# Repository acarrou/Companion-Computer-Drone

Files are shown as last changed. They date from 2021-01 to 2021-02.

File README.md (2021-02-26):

# PX4 Companion-Computer-Drone
## Introduction
This guide is meant to help people interested in making a drone using a Pixhawk as the flight controller with an onboard computer of your choice using Dronekit or ROS. This guide shows you how to use Dronekit using a Raspberry Pi and ROS with a Jetson Nano. However, they can both be done the same way with some changes. There are specific components that are needed to complete this project.

# Table of Contents
- [:one: Getting Started](#one-getting-started)
    - [Parts Required](#parts-required)
    - [Drone Assembly](#drone-assembly)
    - [Firmware](#firmware)
- [:two: The Onboard Computer](#two-the-onboard-computer)
    - [Jetson Nano (***THIS SECTION IS STILL UNDER CONSTRUCTION USE THE RASPBERRY PI FOR NOW***)](#jetson-nano)
        - [ROS Melodic Installation](#ros-melodic-installation)
        - [MAVROS Installation](#mavros-installation)
        - [Pixhawk and Jetson Nano Configuration](#pixhawk-and-jetson-nano-configuration)
        - [Jetson Nano and Pixhawk Communication](#jetson-nano-and-pixhawk-communication)
    - [Raspberry Pi](#raspberry-pi)
        - [GPIO Pin Configuration](#gpio-pin-configuration)
        - [Raspberry Pi Serial Configuration](#raspberry-pi-serial-configuration)
        - [Raspberry Pi and Pixhawk Communication](#raspberry-pi-and-pixhawk-communication)
        - [Dronekit](#dronekit)
            - [Simulation](#simulation)
            - [Running Dronekit on the Pi](#running-dronekit-on-the-pi)
            
<br><br/>

# :one: Getting Started
## Parts Required
Everything on the ***[Parts List](https://docs.google.com/document/d/1yg1S2lEn6Pxzbmr_OziczwqIsVRe4be1YQAyOio6FKI/edit?usp=sharing)*** is required for this project. Please read carefully what is needed. This is also assuming you have the necessary tools of a soldering iron, snips, and other essential tools needed for electronics.

## Drone Assembly
***[Here](https://youtube.com/playlist?list=PLm_39In9-wKMa8U90cwcDMecCGuM5Sja1)*** is a playlist of videos showing you how to build your drone. This will also go over how to flash the Firmware to the pixhawk. I will go more in-depth regarding the Firmware in the next area. You can choose either Ardupilot or PX4. However, I recommend PX4 Firmware.

Make sure your motors are in the correct configuration. You do this by making sure the motor wires are connected to the correct wires of the ESC. Below is a diagram of the direction of the motors and ESC configuration.
***I recommend you put on the propellers at the end. Not until you are ready to fly.***
<br><br/>

<br><br/>

<br><br/>


<br><br/>
Plug the ESC pins into back of the Pixhawk. (order should be from top-> -, s, +) ***Make sure they are in the correct order or your drone will fly incorrectly.***
<br><br/>

<br><br/>
Plug in the rest of  the modules you've puchased into their respected slots as showed in this image:
<br><br/>


<br><br/>

## Firmware
We are using [QGroundControl](https://docs.qgroundcontrol.com/master/en/getting_started/download_and_install.html), it works great and makes it easy to set parameters. Follow this [video](https://www.youtube.com/watch?v=BNzeVGD8IZI&t=677s) on how to install the PX4 Firmware. If you would like to use the Ardupilot firmware, click on Ardupilot in the QGroundControl options. If you have issues with the latest px4 Firmware, you can look at earlier versions [here](https://github.com/PX4/PX4-Autopilot/releases), we are currently using ***v1.10.1***.


<br><br/>

# :two: The Onboard Computer
There are two companion computers we recommend using the Jetson Nano or the Raspberry Pi. The Jetson Nano is a pricier embedded system compared to the Raspberry Pi. However, it makes an excellent system for object detection/avoidance. Make sure you have all the necessary parts to power and put an OS on these computers. You will need a device to put the OS on the micro sd card. Something like this -> ***[Micro SD Card USB Reader.](https://www.amazon.com/UGREEN-Reader-Portable-Adapter-Windows/dp/B0779V61XB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)*** This makes it easy to image.
<br/>
[nKuylen](https://github.com/nKuylen) has made a platform in the back of the drone for the Raspberry pi or Jetson Nano. We recommend printing this or developing your own.

## Jetson Nano (***THIS SECTION IS STILL UNDER CONSTRUCTION USE THE RASPBERRY PI FOR NOW***)

We will be using ROS with the Jetson Nano. If you are unfamiliar with ROS, I recommend you learn it first through the [documentation](http://wiki.ros.org/Documentation) as this part will assume you know how to operate the catkin workspace. For more information on the Jetson nano, please follow this ***[site](https://developer.nvidia.com/embedded/learn/get-started-jetson-nano-devkit)***. It would be best to use ***[Balena Etcher](https://www.balena.io/etcher/)*** for an easy imaging process. A helpful video I found is ***[here](https://www.youtube.com/watch?v=fepv1uDyiXk)***. Use the image given for the Jetson Nano ***[here](https://developer.nvidia.com/embedded/learn/get-started-jetson-nano-devkit#write)***. Once you have successfully imaged your Jetson Nano put the sd card into the Nano.
### ROS Melodic Installation
We are using ROS Melodic as the Jetson Nano is using their NVIDIA® Jetson Nano™ Developer Kit deriving from Ubuntu 18.04. This ROS install is taken from [here](http://wiki.ros.org/melodic/Installation/Ubuntu)
<br/>

Setting your sources.list
<br/>
```bash
sudo sh -c 'echo "deb http://packages.ros.org/ros/ubuntu $(lsb_release -sc) main" > /etc/apt/sources.list.d/ros-latest.list'
```
<br/>

Keys Setup:
<br/>
```bash
sudo apt-key adv --keyserver 'hkp://keyserver.ubuntu.com:80' --recv-key C1CF6E31E6BADE8868B172B4F42ED6FBAB17C654
```
<br/>

Install:
<br/>
```bash
sudo apt update
sudo apt install ros-melodic-desktop-full
```
<br/>

Environment Setup:
<br/>
```bash
echo "source /opt/ros/melodic/setup.bash" >> ~/.bashrc
source ~/.bashrc
```
<br/>

(Optional) Dependencies for Building Packages:
<br/>
```bash
sudo apt install python-rosdep python-rosinstall python-rosinstall-generator python-wstool build-essential
```
<br/>

Install rosdep:
<br/>
```bash
sudo apt install python-rosdep
```

<br/>
Initialize rosdep:
<br/>

```bash
sudo rosdep init
rosdep update
```
<br><br/>

### MAVROS Installation
***--NEED TO WORK ON THIS--*** <br/>
MAVROS is the MAVLink extendable communication node for ROS with proxy for Ground Control Station.
<br><br/>
Install MAVROS:
<br/>
```bash
sudo apt-get install ros-melodic-mavros ros-melodic-mavros-extras
```
<br><br/>
Install Geographic datasets:
<br/>
```bash
wget https://raw.githubusercontent.com/mavlink/mavros/master/mavros/scripts/install_geographiclib_datasets.sh
chmod a+x install_geographiclib_datasets.sh
sudo ./install_geographiclib_datasets.sh
```
<br><br/>

### Pixhawk and Jetson Nano Configuration
The configuration for the Pixhawk and Jetson Nano is straightforward. Use a micro USB to USB cable. Connect the micro USB side into the Pixhawk's serial port and the USB into the Jetson nano.
<br/>

<br><br/>

### Jetson Nano and Pixhawk Communication
After plugging the cord into the Pixhawk and Nano, you can run this command to see if everything is correct:
<br/>
```bash
roslaunch mavros px4.launch
```
<br/>

If there is a permissions issue with the serial port, make sure your user is in the 'dialout' group. You can do this by using this command (replace the 'enter username' with your username):
<br/>
```bash
sudo usermod -a -G dialout enter username
```
Congrats! You have successfully connected your Nano to your Pixhawk. If you are having trouble, this [video](https://www.youtube.com/watch?v=Irko6xb2qjs) may help you.
<br><br/>

## Raspberry Pi
Start by Installing the Raspberry Pi OS using Raspberry Pi Imager ***[here](https://www.raspberrypi.org/software/)***. Image the Pi with the recommended OS. You can use this ***[video](https://www.youtube.com/watch?v=y45hsd2AOpw)*** to help you image the Pi.

### GPIO Pin Configuration
In order for the Pi to communicate with the Pixhawk, we need to connect four cables. They are 5V, GND, TX, and RX. You will need to create the connector yourself. I purchased this ***[kit](https://www.amazon.com/1-25mm-Connectors-Pre-Crimped-Pixhawk-Silicone/dp/B07S18D3RN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)*** to make my own. I then soldered the connectors from the pixhawk to 4 female jumper wires.

***Here is the configuration of the pins***

<br><br/>

### Raspberry Pi Serial Configuration

On your Raspberry Pi, enter:
```bash
sudo raspi-config
```
And in the utility, select “Interfacing Options”:
<br/>

<br><br/>
RasPiConfiguration Utility
And then “Serial”:
<br/>

<br><br/>
When prompted, select ```no``` to “Would you like a login shell to be accessible over serial?”.

When prompted, select ```yes``` to “Would you like the serial port hardware to be enabled?”.

Reboot the Raspberry Pi when you are done.

The Raspberry Pi’s serial port will now be usable on ```/dev/serial0```.

<br><br/>

### Raspberry Pi and Pixhawk Communication

Once you have configured your Pi, you now have to change a few parameters on your pixhawk in QGroundControl or another ground control software. To set up the default companion computer message stream on TELEM 2, set the following parameters:
```bash
MAV_1_CONFIG = TELEM 2 (MAV_1_CONFIG is often used to map the TELEM 2 port)
MAV_1_MODE = Onboard
SER_TEL2_BAUD = 921600 (921600 or higher recommended for applications like log streaming or FastRTPS)
```

After you have changed those parameters, restart the Pixhawk. If not done already, connect the Raspberry Pi to the Pixhawk. You will need to install MAVProxy dependencies. You can find the MAVProxy install here -> [MAVProxy INSTALL GUIDE](https://ardupilot.org/mavproxy/docs/getting_started/download_and_installation.html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). I will show below how to install these dependencies for Python 2 since that is what the Pi has on default.

For Python 2 on Debian based systems (including Ubuntu, WSL, Raspian):
<br/>
```bash 
sudo apt-get install python-dev python-opencv python-wxgtk4.0 python-pip python-matplotlib python-lxml python-pygame
pip install PyYAML mavproxy --user
echo "export PATH=$PATH:$HOME/.local/bin" >> ~/.bashrc
```

If you get a “permission denied” error message when connecting to serial devices, the user permissions may need to be changed:
<br/>
```bash 
sudo usermod -a -G dialout <username>
```

Make sure you update:
<br/>
```bash
pip install mavproxy --user --upgrade
```
Once finished installing everything, make sure to reboot the Pi.
<br><br/>

Next, run this command in the terminal to test the serial connection between the Pi and Pixhawk. If you are only getting the ```MAV>``` sign, make sure your parameters are correct for baud rate and correct telemetry port. It could also be your gpio pins are incorrect or not fully pushed on the RPI.
<br/>
Enter this command to test:
<br/>
```bash
mavproxy.py --master=/dev/serial0 --baudrate 921600 --aircraft MyCopter
``` 
You should see something like this:
<br/>

<br/>
You can also arm and test the throttle by typing :
<br/>
***MAKE SURE YOUR PROPS ARE OFF BEFORE!*** 
```bash
arm throttle
```

Then check to see if the pi can communicate with a computer using QGroundControl (Your Computer's IP running QGC)
```bash
mavproxy.py --master=/dev/serial0 --baudrate 921600 --out <Computer IP>:14550 --aircraft MyCopter 
```
<br><br/>

### Dronekit
#### **Simulation**
If simulating the drone using Dronekit to test scripts is something you're interested in following along. Otherwise, proceed to the Dronekit Installation on the Pi. We are using Ubuntu 18.04, but any other Ubuntu version should work.
<br><br/>

Clone the PX4 source code:
<br/>
```bash
git clone https://github.com/PX4/PX4-Autopilot.git --recursive
```
<br/>

Enter the directory:
<br/>

```bash
cd PX4-Autopilot/
```
<br/>

Install:
<br/>
```bash
bash ./Tools/setup/ubuntu.sh
```
<br/>

Check to see if you can run the Simulation on your Linux machine.
<br/>
Enter the directory:
<br/>

```bash
cd PX4-Autopilot/
```
<br/>

Choose from either Gazebo or jMAVSim:
<br/>
```bash
make px4_sitl_default jmavsim
```
OR 
<br/>

```bash
make px4_sitl gazebo
```
<br/>

In your Linux terminal, clone the Dronekit repository using:
<br/>
```bash
git clone https://github.com/dronekit/dronekit-python.git
```
<br/>
Enter the directory:
<br/>

```bash
cd ./dronekit-python
```
<br/>
Then build and install:
<br/>

```bash
sudo python setup.py build
sudo python setup.py install
```

While the Simulation is running in the background, you can use an IDE of your choice (We are using Pycharm). In the IDE, go to the directory and use the interpreter from the dronekit repository. Then run this code below that uses the Dronekit library.
<br/>
[Dronekit Mission Simulation Example](https://github.com/acarrou/Companion-Computer-Drone/blob/main/Dronekit-Scripts/DronekitMissionSimEx.py)
<br/>
Notice the code uses the IP - '127.0.0.1:14540' as this is the simulation's IP. Run the code and see it take off!
<br><br/>

#### **Running Dronekit on the Pi**
In your Raspberry Pi's terminal, enter these commands:

Update Pi
```bash
sudo apt-get update
sudo apt-get upgrade
```
Install Dronekit, and Dependencies
```bash
sudo apt-get install python-pip python-dev
sudo pip install pyserial
sudo pip install dronekit
sudo pip install MAVProxy
```
<br/>

Create a folder where you can put your dronekit scripts. Take the code from [Dronekit Mission Real Example](https://github.com/acarrou/Companion-Computer-Drone/blob/main/Dronekit-Scripts/DronekitMissionRealEx.py). Notice the connection string is different from the IP we had before in the Simulation. We also had to specify the baud rate in the vehicle initialization on line 40 for our pixhawk and Pi to communicate. Now that we have the code set up, lets run the program!
<br><br/>

Run Command:
<br/>
***ATTENTION! THIS PROGRAM ARMS THE DRONE AND EXECUTES THE PATH***
<br/>
```bash
python DronekitMissionRealEx.py --connect /dev/serial0
```
<br/>

You now have a drone running with Dronekit! For more information on Dronekit, visit their documentation page [here](https://dronekit-python.readthedocs.io/en/latest/about/index.html).

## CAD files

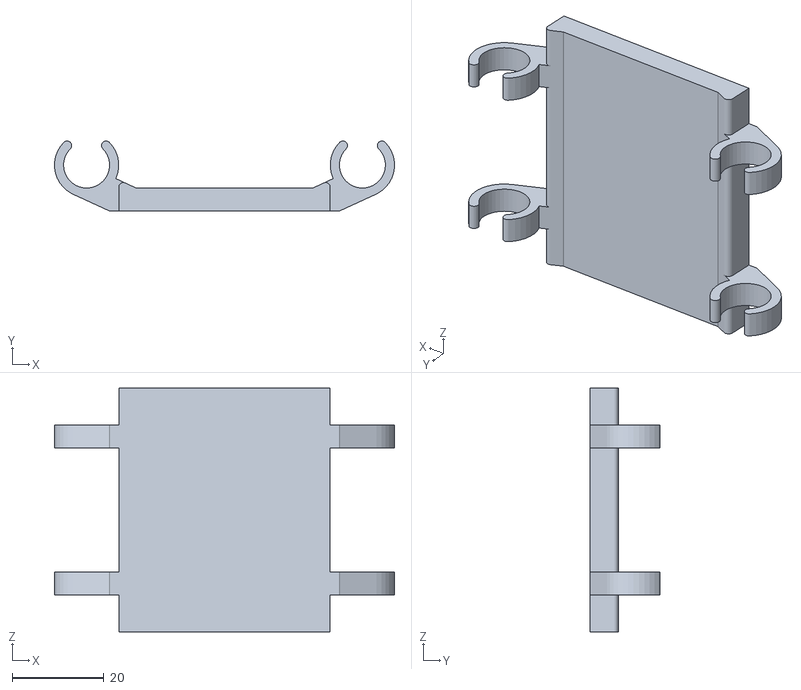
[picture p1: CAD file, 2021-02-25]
Drone Back Platform.STL
74.0 x 15.2 x 53.0

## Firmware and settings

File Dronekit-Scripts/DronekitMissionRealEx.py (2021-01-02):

################################################################################################
# @File DroneKitPX4.py
# Example usage of DroneKit with PX4
#
# @author Sander Smeets <sander@droneslab.com>
#
# Code partly based on DroneKit (c) Copyright 2015-2016, 3D Robotics.
################################################################################################

# Import DroneKit-Python
from dronekit import connect, Command, LocationGlobal
from pymavlink import mavutil
import time, sys, argparse, math


################################################################################################
# Settings
################################################################################################

connection_string   = '/dev/serial0'
MAV_MODE_AUTO   = 4
# https://github.com/PX4/PX4-Autopilot/blob/master/Tools/mavlink_px4.py


# Parse connection argument
parser = argparse.ArgumentParser()
parser.add_argument("-c", "--connect", help="connection string")
args = parser.parse_args()

if args.connect:
    connection_string = args.connect


################################################################################################
# Init
################################################################################################

# Connect to the Vehicle
print "Connecting"
vehicle = connect(connection_string, wait_ready=True, baud=921600)

def PX4setMode(mavMode):
    vehicle._master.mav.command_long_send(vehicle._master.target_system, vehicle._master.target_component,
                                               mavutil.mavlink.MAV_CMD_DO_SET_MODE, 0,
                                               mavMode,
                                               0, 0, 0, 0, 0, 0)



def get_location_offset_meters(original_location, dNorth, dEast, alt):
    """
    Returns a LocationGlobal object containing the latitude/longitude `dNorth` and `dEast` metres from the
    specified `original_location`. The returned Location adds the entered `alt` value to the altitude of the `original_location`.
    The function is useful when you want to move the vehicle around specifying locations relative to
    the current vehicle position.
    The algorithm is relatively accurate over small distances (10m within 1km) except close to the poles.
    For more information see:
    http://gis.stackexchange.com/questions/2951/algorithm-for-offsetting-a-latitude-longitude-by-some-amount-of-meters
    """
    earth_radius=6378137.0 #Radius of "spherical" earth
    #Coordinate offsets in radians
    dLat = dNorth/earth_radius
    dLon = dEast/(earth_radius*math.cos(math.pi*original_location.lat/180))

    #New position in decimal degrees
    newlat = original_location.lat + (dLat * 180/math.pi)
    newlon = original_location.lon + (dLon * 180/math.pi)
    return LocationGlobal(newlat, newlon,original_location.alt+alt)





################################################################################################
# Listeners
################################################################################################

home_position_set = False

#Create a message listener for home position fix
@vehicle.on_message('HOME_POSITION')
def listener(self, name, home_position):
    global home_position_set
    home_position_set = True



################################################################################################
# Start mission example
################################################################################################

# wait for a home position lock
while not home_position_set:
    print "Waiting for home position..."
    time.sleep(1)

# Display basic vehicle state
print " Type: %s" % vehicle._vehicle_type
print " Armed: %s" % vehicle.armed
print " System status: %s" % vehicle.system_status.state
print " GPS: %s" % vehicle.gps_0
print " Alt: %s" % vehicle.location.global_relative_frame.alt

# Change to AUTO mode
PX4setMode(MAV_MODE_AUTO)
time.sleep(1)

# Load commands
cmds = vehicle.commands
cmds.clear()

home = vehicle.location.global_relative_frame

# takeoff to 10 meters
wp = get_location_offset_meters(home, 0, 0, 10);
cmd = Command(0,0,0, mavutil.mavlink.MAV_FRAME_GLOBAL_RELATIVE_ALT, mavutil.mavlink.MAV_CMD_NAV_TAKEOFF, 0, 1, 0, 0, 0, 0, wp.lat, wp.lon, wp.alt)
cmds.add(cmd)

# move 10 meters north
wp = get_location_offset_meters(wp, 10, 0, 0);
cmd = Command(0,0,0, mavutil.mavlink.MAV_FRAME_GLOBAL_RELATIVE_ALT, mavutil.mavlink.MAV_CMD_NAV_WAYPOINT, 0, 1, 0, 0, 0, 0, wp.lat, wp.lon, wp.alt)
cmds.add(cmd)

# move 10 meters east
wp = get_location_offset_meters(wp, 0, 10, 0);
cmd = Command(0,0,0, mavutil.mavlink.MAV_FRAME_GLOBAL_RELATIVE_ALT, mavutil.mavlink.MAV_CMD_NAV_WAYPOINT, 0, 1, 0, 0, 0, 0, wp.lat, wp.lon, wp.alt)
cmds.add(cmd)

# move 10 meters south
wp = get_location_offset_meters(wp, -10, 0, 0);
cmd = Command(0,0,0, mavutil.mavlink.MAV_FRAME_GLOBAL_RELATIVE_ALT, mavutil.mavlink.MAV_CMD_NAV_WAYPOINT, 0, 1, 0, 0, 0, 0, wp.lat, wp.lon, wp.alt)
cmds.add(cmd)

# move 10 meters west
wp = get_location_offset_meters(wp, 0, -10, 0);
cmd = Command(0,0,0, mavutil.mavlink.MAV_FRAME_GLOBAL_RELATIVE_ALT, mavutil.mavlink.MAV_CMD_NAV_WAYPOINT, 0, 1, 0, 0, 0, 0, wp.lat, wp.lon, wp.alt)
cmds.add(cmd)

# land
wp = get_location_offset_meters(home, 0, 0, 10);
cmd = Command(0,0,0, mavutil.mavlink.MAV_FRAME_GLOBAL_RELATIVE_ALT, mavutil.mavlink.MAV_CMD_NAV_LAND, 0, 1, 0, 0, 0, 0, wp.lat, wp.lon, wp.alt)
cmds.add(cmd)

# Upload mission
cmds.upload()
time.sleep(2)

# Arm vehicle
vehicle.armed = True

# monitor mission execution
nextwaypoint = vehicle.commands.next
while nextwaypoint < len(vehicle.commands):
    if vehicle.commands.next > nextwaypoint:
        display_seq = vehicle.commands.next+1
        print "Moving to waypoint %s" % display_seq
        nextwaypoint = vehicle.commands.next
    time.sleep(1)

# wait for the vehicle to land
while vehicle.commands.next > 0:
    time.sleep(1)


# Disarm vehicle
vehicle.armed = False
time.sleep(1)

# Close vehicle object before exiting script
vehicle.close()
time.sleep(1)

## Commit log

2021-01-01 Full mission example
    The following python script shows a full mission example using DroneKit and PX4. Mode switching is not yet fully supported by DroneKit. We, therefore, send our own custom mode switching commands. Thi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
2021-01-16 Update README.md
    arm throttle test and helpful image
2021-02-25 Drone back plate addition
    [Drone Back Platform.STL]
